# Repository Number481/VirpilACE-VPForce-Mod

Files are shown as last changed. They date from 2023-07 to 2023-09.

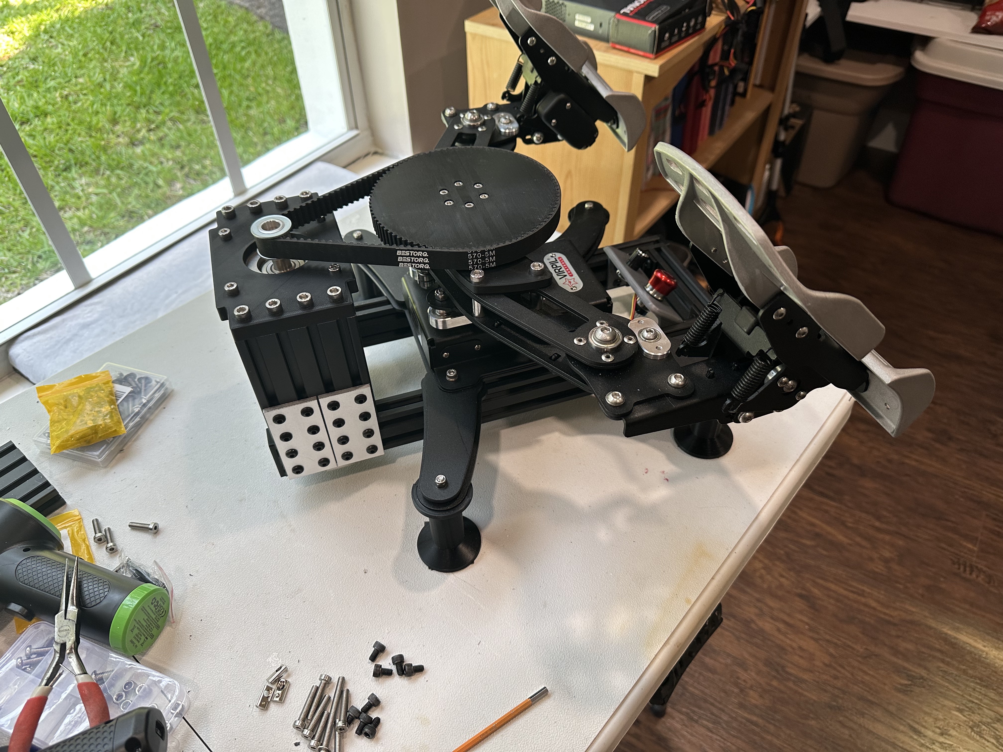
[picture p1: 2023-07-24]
Photos/IMG_0804.jpeg

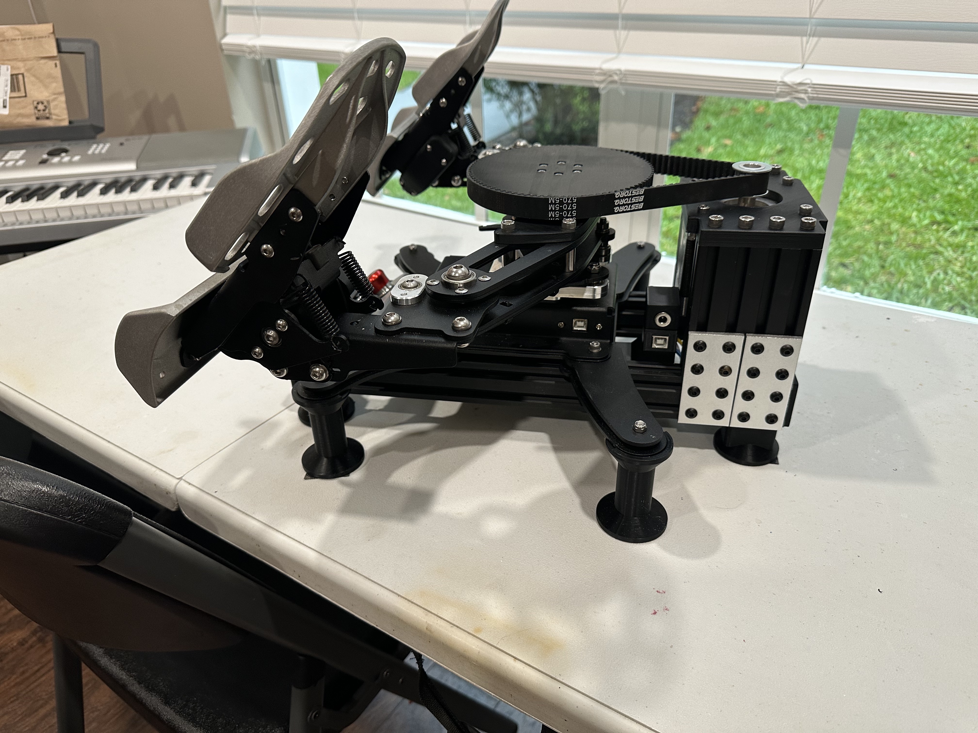
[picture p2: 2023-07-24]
Photos/IMG_0811.jpeg

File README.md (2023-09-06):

# Virpil ACE | VPForce FFB Mod

This repository contains the design files for my VPForce DIY Force Feedback Kit modification of the Virpil ACE pedals.

VPF_VPC-Pedals

The build can be completed without making any permanent modifications to the pedals.  There are 3x M6 holes in the main pulley and pulley mounting plate that can be used to secure the center of the plate to the upper arm if you so desire, but that will require drilling 3x 6mm holes in the upper arm of the pedals.  These bolts are not required and , to date, I have not installed them on my build.

## Tracked Changes
Sept 9, 2023
- Added updated control mount STL file that mirrors the key/notch for the potentiometer orientation
- Added updated main pulley mounting plate which has a recess to account for variences in the pedal manufacturing where the main center axis bolt head can protrude above the pedal arms
- Corrected the hardware in the build sheet for attaching the main pedal assembly to the 2040 rails from m5x25 to m5x20

## CYA Note:
The Virpil ACE pedals 3D model that is part of these design files is of my own making.  It was not provided by, nor does it have any affiliation with Virpil.  The only truly accurate aspects of the model are the 130x135mm bolt pattern of the base and the M6 mounting hole locations where the gear mount attaches to the upper pedal arms.  The remainder of the parts are drawn by me using rough measurements and eye-balling.

Any potential long term affects of the lateral forces being applied to the bearings of the Virpil pedals are unknown.

***Modify your pedals at your own risk***
## Primary Components:
- Virpil Ace Pedals
- VPForce 86BLF03 single motor kit
- Various Aluminum Extrusion sizes and lengths
- Assorted T-slot hardware (t-nuts, angle brackets, join plates)
- Various 3D printed parts
- A suitable timing belt
- A suitable drive pulley
- Assorted wire for power plug and shutoff switch / potentiometer (~14-16AWG for power and ~22AWG for pot)
- JST-HX connector and crimping tools for potentiometer->control board connection.  You can also find long pre-terminated pigtails on amazon.  The pigtail that comes pre-attached to most Pots is not long enough.

# Pedals in Action:
IMAGE ALT TEXT HERE (https://www.youtube.com/watch?v=AWd7LjSCXhk)

# What do I need?
A full as-built build list is provided in the repository:
** Updated Sept,9 2023
VPF_VPC-Pedals_Build List

The above list covers the majority of what you will need to build this project. Other things you will probably need include but are not necessarily limited to:
- Ability to cut the aluminum extrusion
    - A miter saw with an aluminum/non-ferrous metal cutting blade works well
- Ability to solder and/or the tools necessary for crimping JST plugs
- Various tools necessary for construction (Alan wrenches, etc)
- M6 Tap set required to thread the end-holes of the 2080 extrusion for the motor mount

# Build Notes
The following is a mostly unstructured brain dump for the build where I think things may require some explanation.

For the most part, it should be apparent in the assembly STEP file how things go together but there are a few things
might not make sense at first glance.  Hopefully I can cover those in the ramblings below.

- The design as built is using a 6:1 gear ratio, with a 15 tooth drive pulley and a 90 tooth main pulley.  With the 
86BLF-03 motor kit from VPForce, I am able to achieve greater resistance at %60 spring force (in the configuration software) than the Virpil pedals can provide with the heaviest springs installed.
    - Because of the way the Virpil base attaches to the 2040 rails, it would be easy to experiment with different gear ratios and belt lengths.
    - It may also be possible to use the stronger 86BLF-04 motor, but you may need to move the frame cross brace that 
sits below the motor (due to the extended motor length).  However, as previously stated, the '03' motor provides ample forces.

- The arms that hold the springs on the pedals also serve as a throw limiter.  If you remove the arms (to stop them 
flopping around with no springs installed), the end-to-end throw of the pedals will increase significantly and be far too much.
    - There are printable throw limiters in the project files and a picture in the photos folder which shows where/how they are installed.
The notch in the limiters is to aid in installation and should face outwards when installed.  I recommend you print them
at %100 infill.

- The control box is designed to be a tight fit for the control board and wiring.  You will likely need to shorten the 
pigtail that comes attached to the USB connector in the VPForce kit in order to get it all to fit in the enclosure.
    - The 3D printed cable grommets are not the best design, and aren't strictly required.  They are a pain to get in place 
with the wiring while you are attaching the back plate, but they do help keep things nice and tidy.
- If you have hard flooring and are looking for a way to secure the pedals, I cant speak highly enough of the Airstick micro-suction 'tape'
from Sewell (https://sewelldirect.com/products/airstick-microsuction-tape). I have hardwood in my office and a small square of this under each foot keeps the pedals *firmly* in place, yet it is possible to pry them up for cleaning and then re-stick to the floor.   You can generally find small quantities for sale on their site or on Amazon.

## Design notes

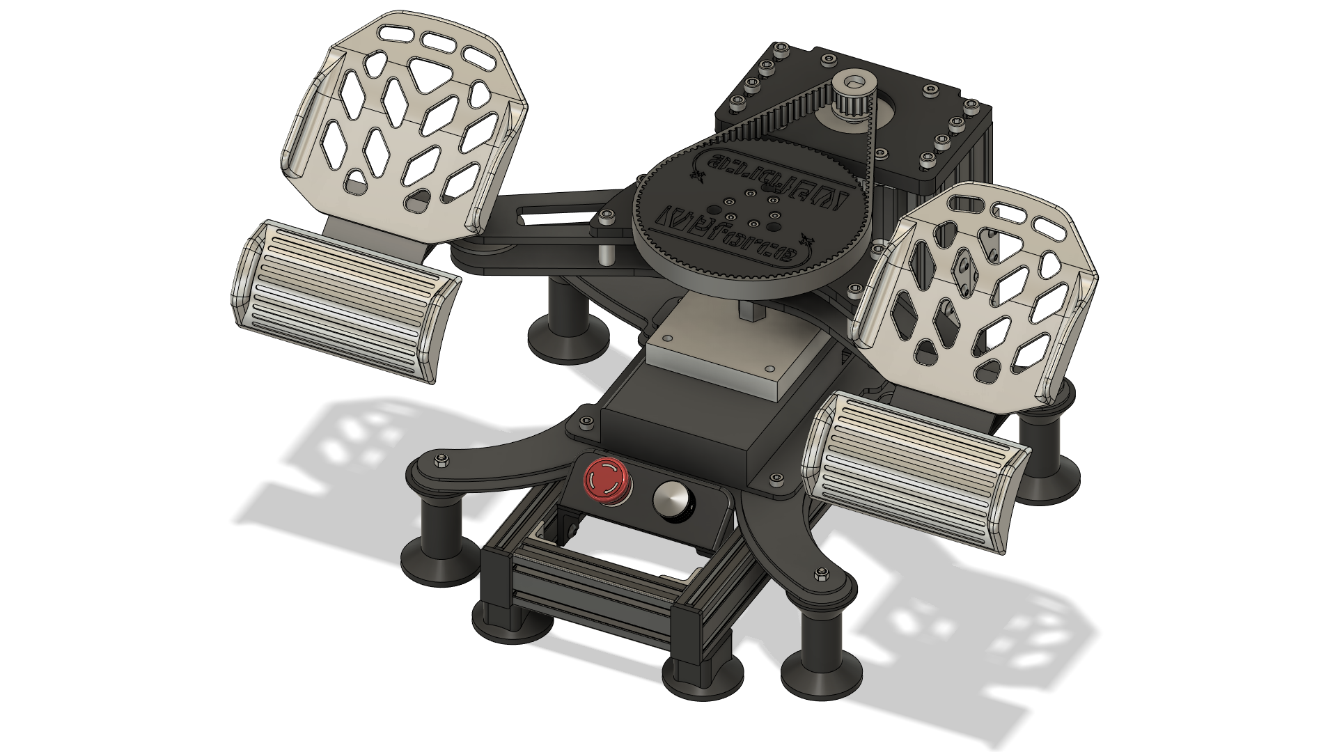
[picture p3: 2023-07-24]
Photos/VPF_VPC-Pedals.png

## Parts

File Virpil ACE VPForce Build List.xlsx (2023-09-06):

Printed Parts List
Part | File | Quantity
Main Pulley | Main-Pulley_90T.stl | Qty 1
 | Gear_Mounting_Plate.stl | Qty 1
Motor Mount | Motor_Mount.stl | Qty 1
Control Board Enclosure | Control_Box.stl | Qty 1
 | Control_Box_Cover.stl | Qty 1
 | Cable_Gromet-H1.stl | Qty 2
 | Cable_Gromet-H2.stl | Qty 2
 | USB Mount.stl | Qty 1
Throw Limiter | Throw_Limiter.stl | Qty 2
Spacer | Spacer.stl | Qty 8
Legs | Virpil_Leg.stl | Qty 4
 | 2040_Leg.stl | Qty 4
Endcaps | 2040-Endcap.stl | Qty 4
Control Mount | Control_Mount.stl | Qty 1
As-Built Hardware List
Part | Description | Quantity | Link
86BLF03 VPForce Kit |  | Qty 1 | https://vpforcecontrols.com/
Drive Pulley | 15T, 12.7mm, HTD5 | Qty 1 | https://www.amazon.com/gp/product/B00J9TUH74
Drive Belt | 570mm 114T, HTD5 | Qty 1 | https://www.amazon.com/gp/product/B09TCZ59TX
Power Supply | 24v 10A | Qty 1 | https://www.amazon.com/gp/product/B0993V49LH
Power Connector | 5.5x2.5mm Female | Qty 1 | https://www.amazon.com/gp/product/B07Y8KKSR1
2040 T-Slot Extrusion | 400mm pieces | Qty 2 | https://www.amazon.com/gp/product/B099NBK1TD
 | 110mm pieces | Qty 2
2080 T-Slot Extrusion | 105mm pieces | Qty 2 | https://www.amazon.com/gp/product/B0B7HQRQ5G
90 Degree Bracket - 2040 |  | Qty 4 | https://www.amazon.com/gp/product/B09ZX28MXY
8 Hole Joining Plates |  | Qty 4 | https://www.amazon.com/gp/product/B0BNMDRH16
Emergency Stop Switch |  | Qty 1 | https://www.amazon.com/gp/product/B07WTL3KPB
Potentiometer | 10K Ohm | Qty 1 | https://www.amazon.com/gp/product/B082FCRQS2
Potentiometer Knob |  | Qty 1 | https://www.amazon.com/gp/product/B07FVH1GR3
T-Slot Nuts - M5 | M5 | Qty 100ish | https://www.amazon.com/gp/product/B07PPYJTPG
M4x20mm | Main Pulley Attach | Qty 6
M4 Lock Nut | Main Pulley Attach | Qty 6
M5x8mm | Frame construction | Qty 50ish | https://www.amazon.com/gp/product/B07F2X6KPG
M5x10mm | 2040 Feet Attach | Qty 4
M5x20mm | Virpil Base Attach | Qty 4
M5x35mm | Virpil Feet Attach | Qty 4
M5 Lock Nut | Virpil Feet Attach | Qty 4
M6x16mm | Pulley Plate Attach | Qty 4
M6x20mm Low Profile | Motor Mount to Plate | Qty 4
M6x20mm | Motor Plate to Frame | Qty 8
Wiring for power plug | 14 - 16 AWG |  | https://www.amazon.com/gp/product/B07FMTCHC1
Wiring for e-stop switch
Wiring for potentiometer | 22 AWG |  | https://www.amazon.com/gp/product/B0B8CCXMWH
JST Connector | JST-HX 3 pin | Qty 1

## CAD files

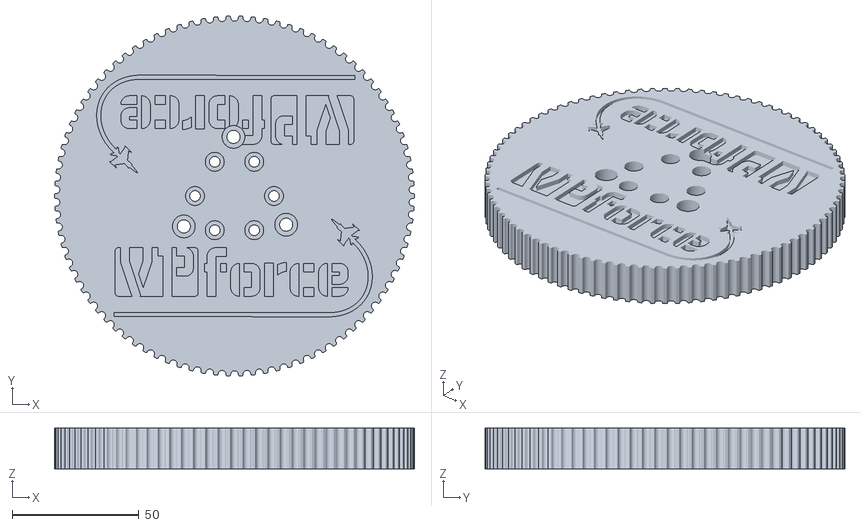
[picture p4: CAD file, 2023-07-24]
STLs/Main-Pulley_90T.stl
142.1 x 142.0 x 16.0

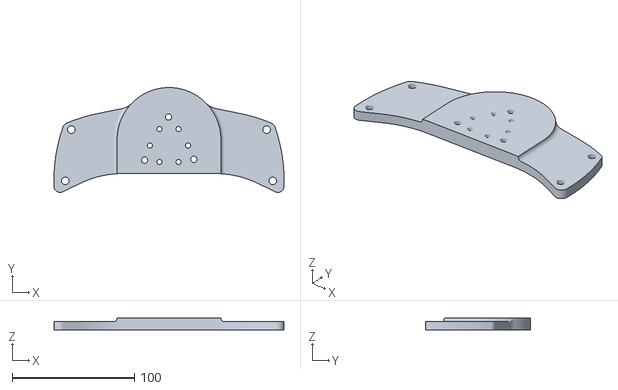
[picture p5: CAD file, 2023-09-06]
STLs/Gear_Arm_Mount_recessed.stl
188.5 x 85.9 x 10.0

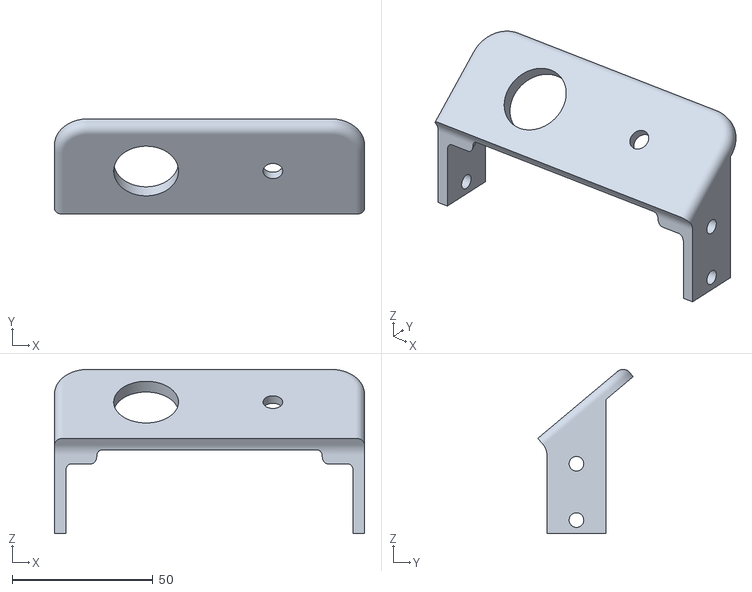
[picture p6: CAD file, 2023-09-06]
STLs/Control_Mount_updated.stl
110.0 x 33.9 x 58.3

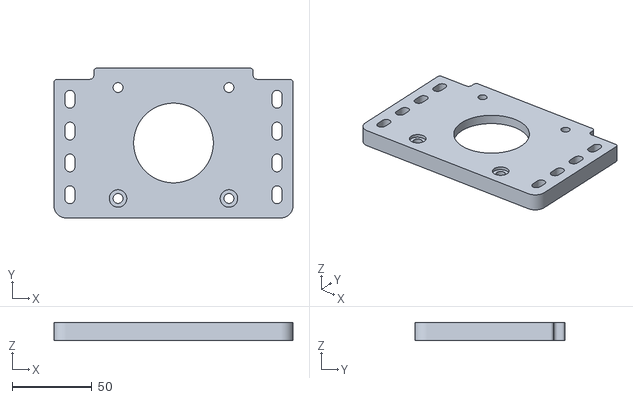
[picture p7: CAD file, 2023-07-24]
STLs/Motor_Mount.stl
150.0 x 94.0 x 11.5

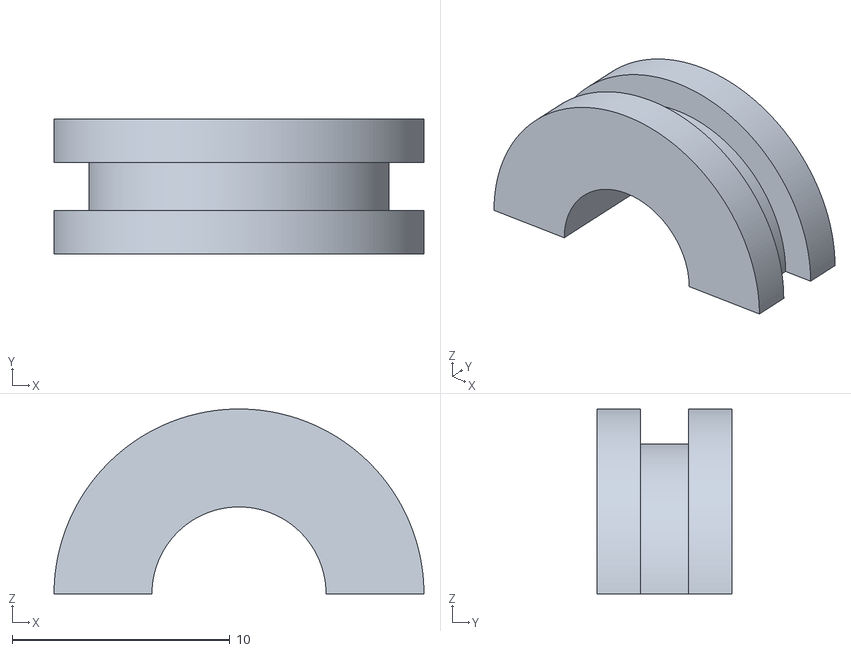
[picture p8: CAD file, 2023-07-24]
STLs/Cable_Gromet-H1(x2).stl
17.0 x 6.20 x 8.50

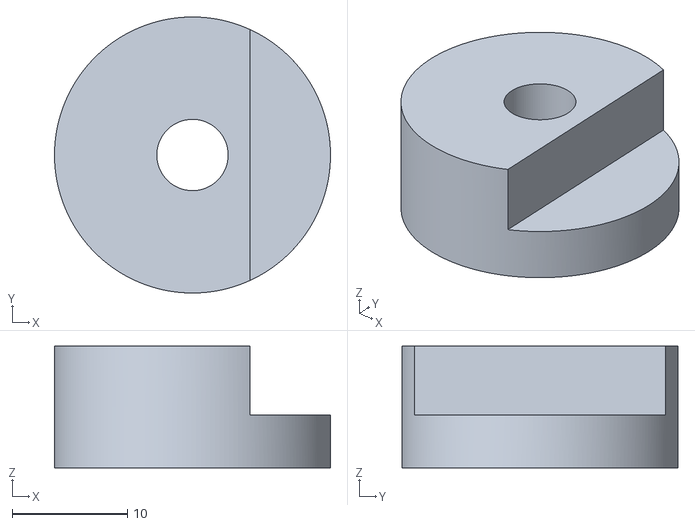
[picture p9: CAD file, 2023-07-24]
STLs/Throw_Limiter(x2).stl
24.0 x 24.0 x 10.6

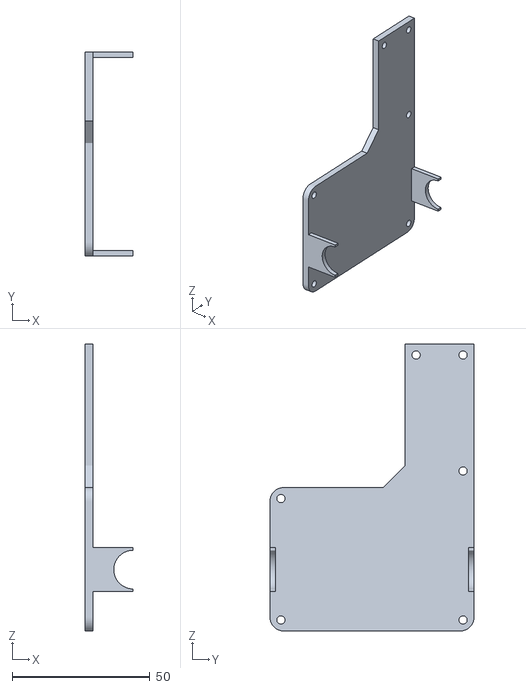
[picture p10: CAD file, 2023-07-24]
STLs/Control_Box_Cover.stl
17.5 x 74.0 x 104.0

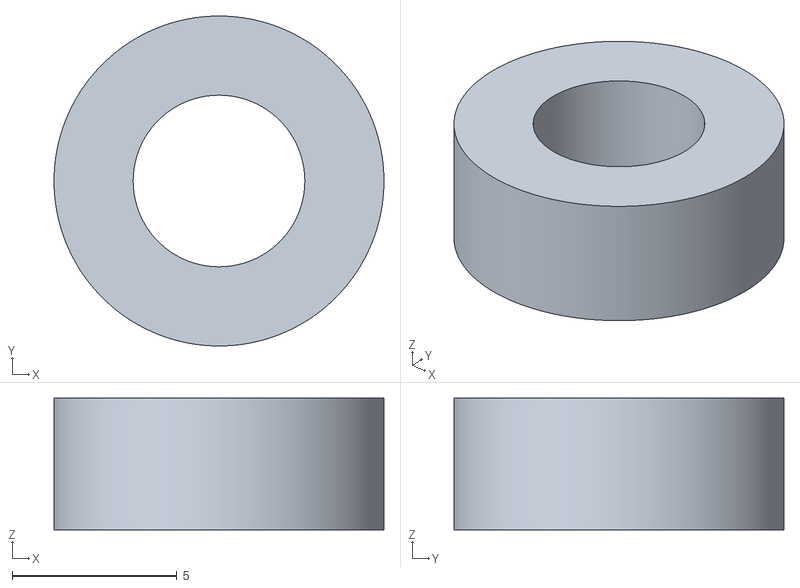
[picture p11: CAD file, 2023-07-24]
STLs/Spacer(x8).stl
10.0 x 10.0 x 4.00

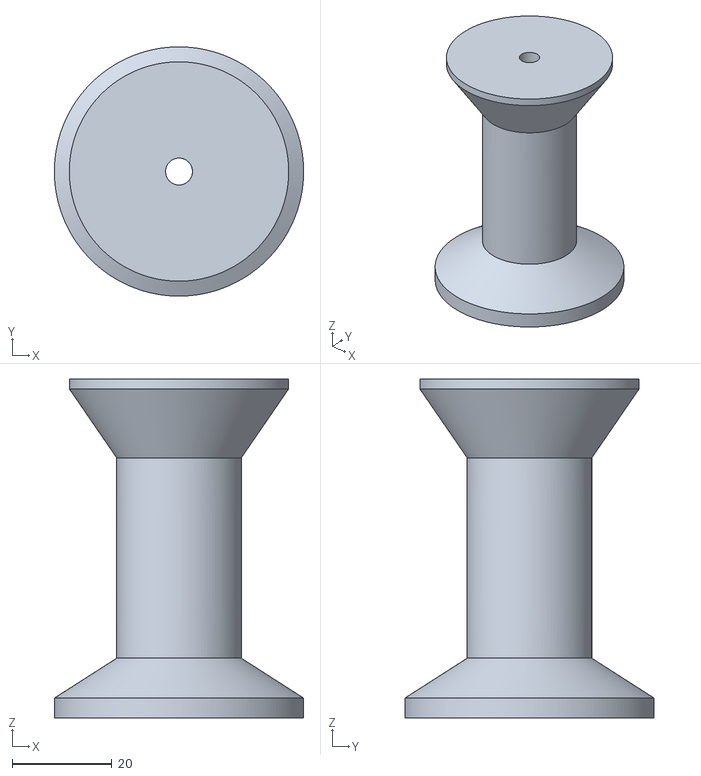
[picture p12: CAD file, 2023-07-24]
STLs/Virpil_Leg(x4).stl
50.0 x 50.0 x 68.0

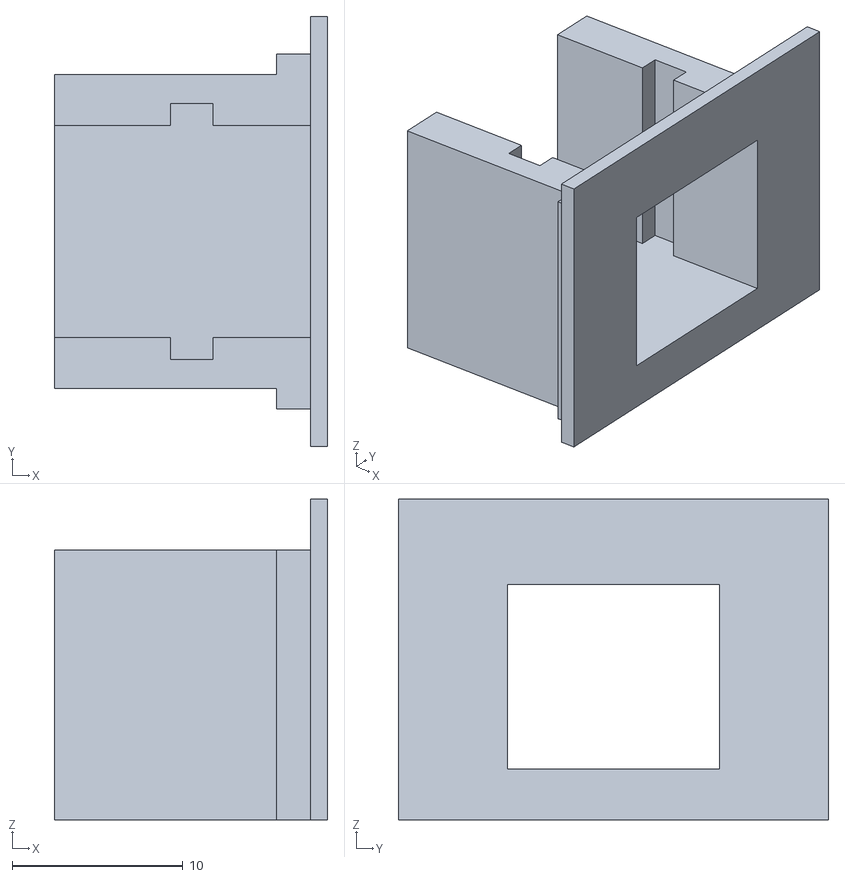
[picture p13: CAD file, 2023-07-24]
STLs/USB Mount.stl
16.0 x 25.2 x 18.8

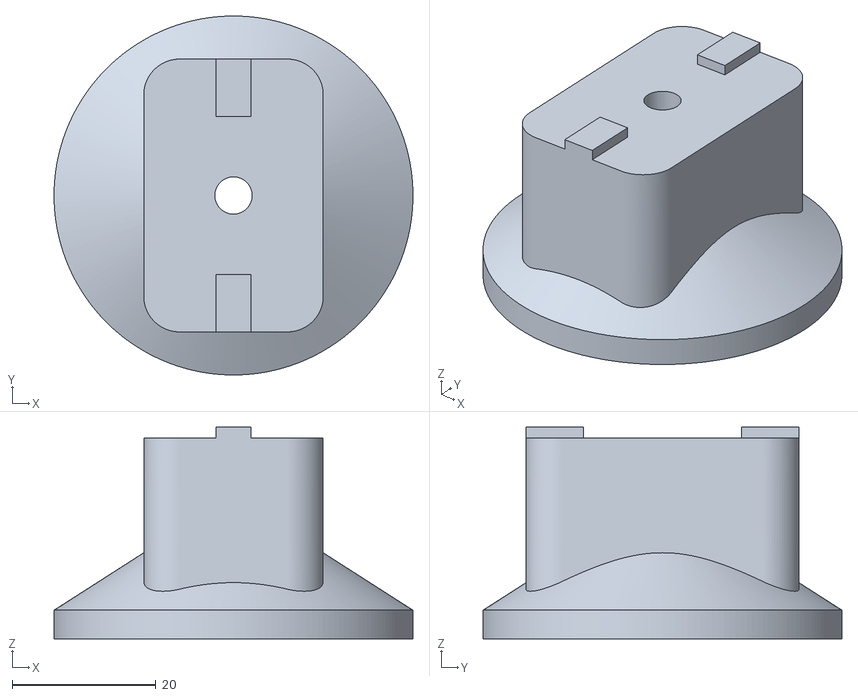
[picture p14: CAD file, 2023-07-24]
STLs/2040_Leg(x4).stl
50.0 x 50.0 x 29.5

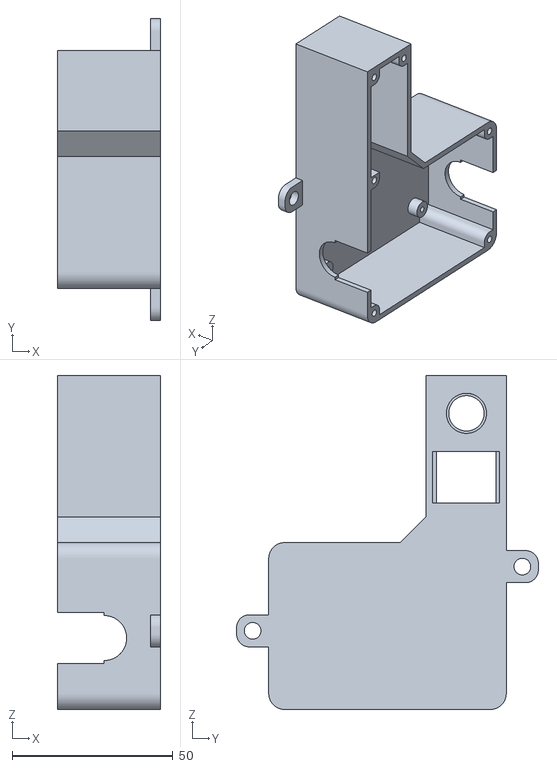
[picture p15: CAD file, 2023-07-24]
STLs/Control_ Box.stl
32.0 x 94.0 x 104.0

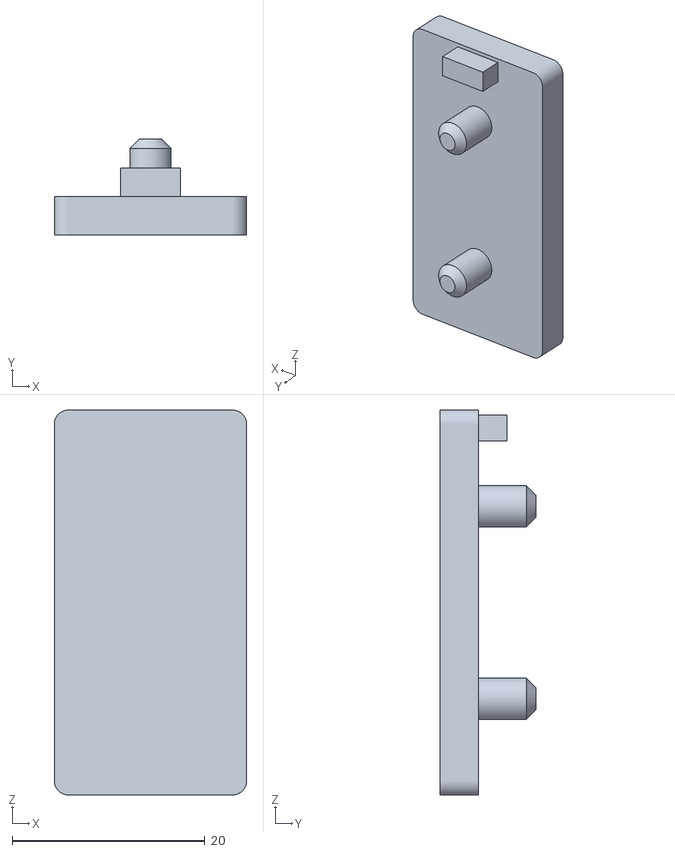
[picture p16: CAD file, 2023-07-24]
STLs/2040-Endcap(x4).stl
20.0 x 10.0 x 40.0

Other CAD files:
STLs/Gear_Mounting_Plate.stl
STLs/Control_Mount.stl
STLs/Cable_GrometH2(x2).stl

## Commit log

2023-07-25 Update Build List FIle
    [Virpil ACE VPForce Build List.xlsx]
2023-07-25 Update Build List
    [Virpil ACE VPForce Build List.xlsx]
2023-09-06 Add updated control mount
    mirror the potentiometer whole key slot to account for different potentiometer orientations
    [Control_Mount_updated.stl]
2023-09-06 Add updated main pulley mount
    Account for assembly variances on pedals where the main center pivot bolt might extrude slightly from the main arms
    [Gear_Arm_Mount_recessed.stl]
2023-09-06 Update build hardware
    [Virpil ACE VPForce Build List.xlsx]
